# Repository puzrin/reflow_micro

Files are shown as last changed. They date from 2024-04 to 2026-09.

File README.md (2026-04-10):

Reflow Micro Table
==================

> Compact Bluetooth-controlled reflow table with an 80x70 mm working area.
> Built for hobby projects when you do not want a bulky professional machine
> taking over your desk.

- [Documentation](doc/README.md)
- [EasyEDA project page](https://oshwlab.com/puzrin/reflow-table-pd) -
  Schematic & PCB. Order almost everything in a couple of clicks.
- [Hackaday.io](https://hackaday.io/project/204503-reflow-micro-table) page.

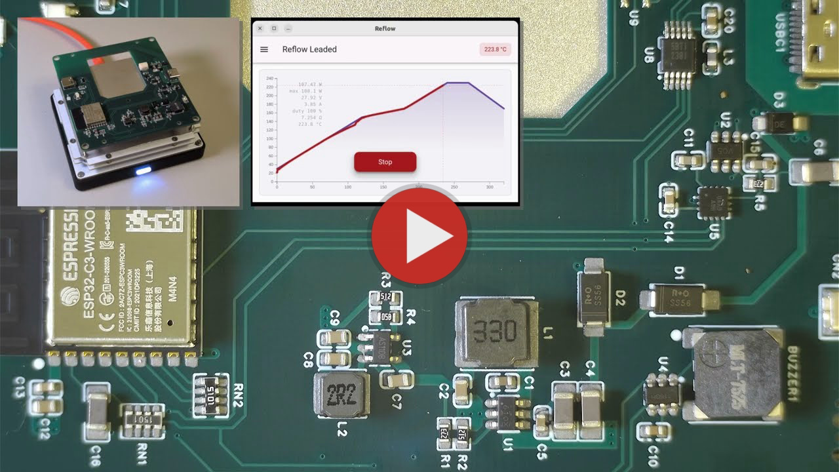
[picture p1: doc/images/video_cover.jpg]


## Description

This table is meant for hobbyists who assemble PCBs from time to time. It may
not be as feature-packed as professional gear, but it's compact and covers most
hobby needs.

Key points:

- Very compact and easy to store when not in use.
- Powered from a 100-140 W USB PD charger.
- Controlled from a web browser (desktop and mobile).
- 80x70 mm working area.
- Components cost about 85$ with the simple MCPCB heater, 105$ with the MCH
  heater.
- Simple heating profile management.
- Up to 180°C with the simple MCPCB-based head.
- Up to 250°C with the MCH-based head.

Use cases:

- Reflow soldering with Sn42Bi58 (138°C) paste using the MCPCB-based head.
- Pre-heating (130-150°C) for hot air work.
- Reflow soldering with Sn63Pb37 (183°C) paste using the MCH-based head.
- Other tinkering, like drying parts or baking paint.

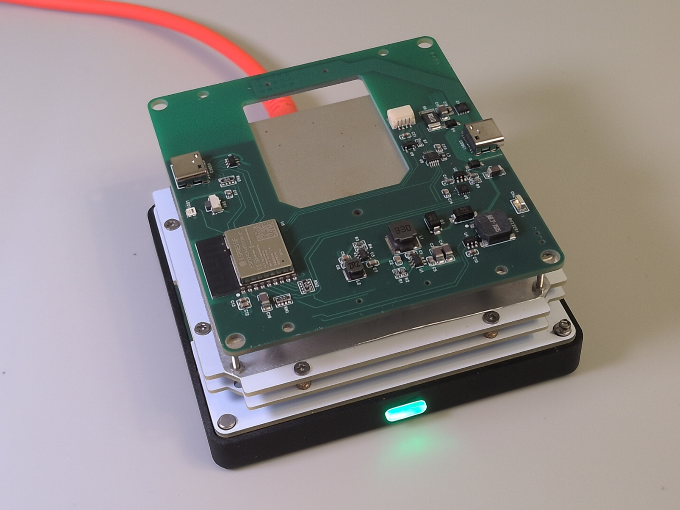
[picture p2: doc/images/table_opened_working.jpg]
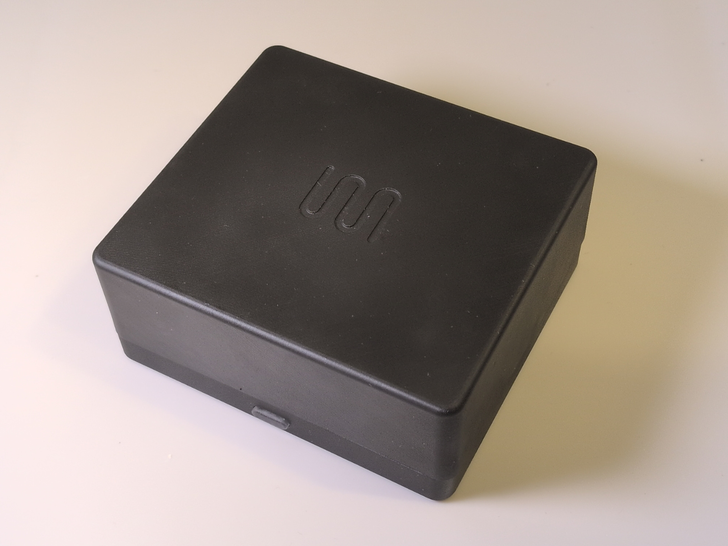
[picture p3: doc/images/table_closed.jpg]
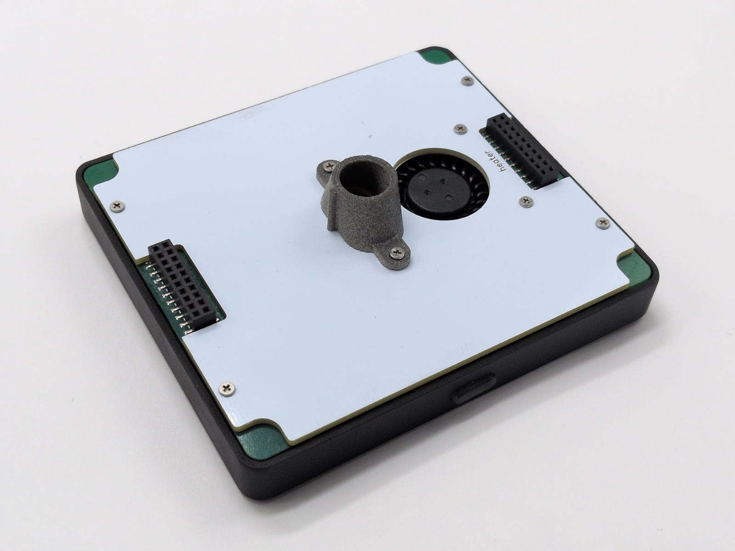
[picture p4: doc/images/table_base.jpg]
  <br />
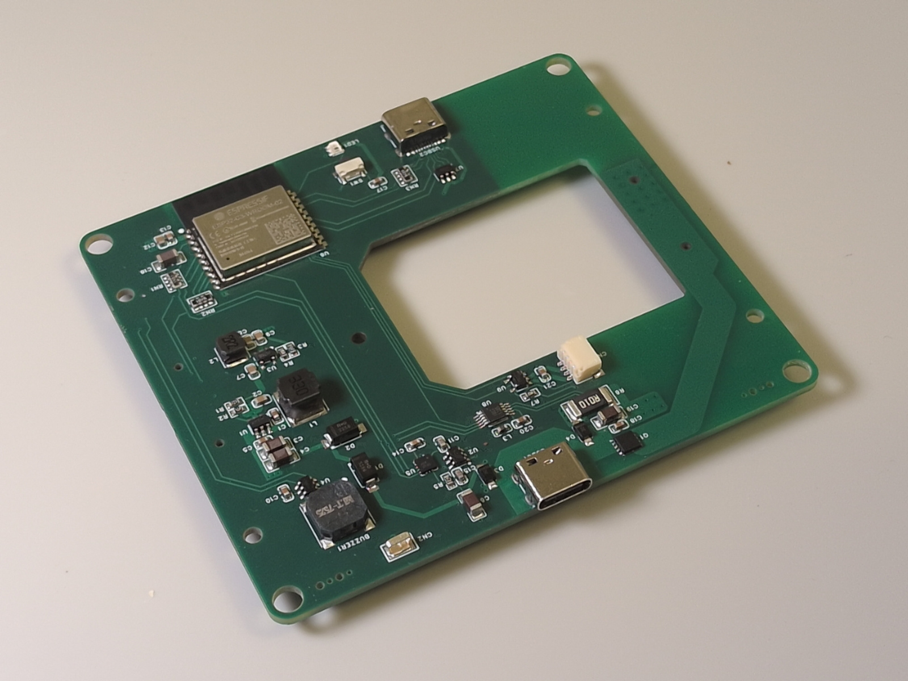
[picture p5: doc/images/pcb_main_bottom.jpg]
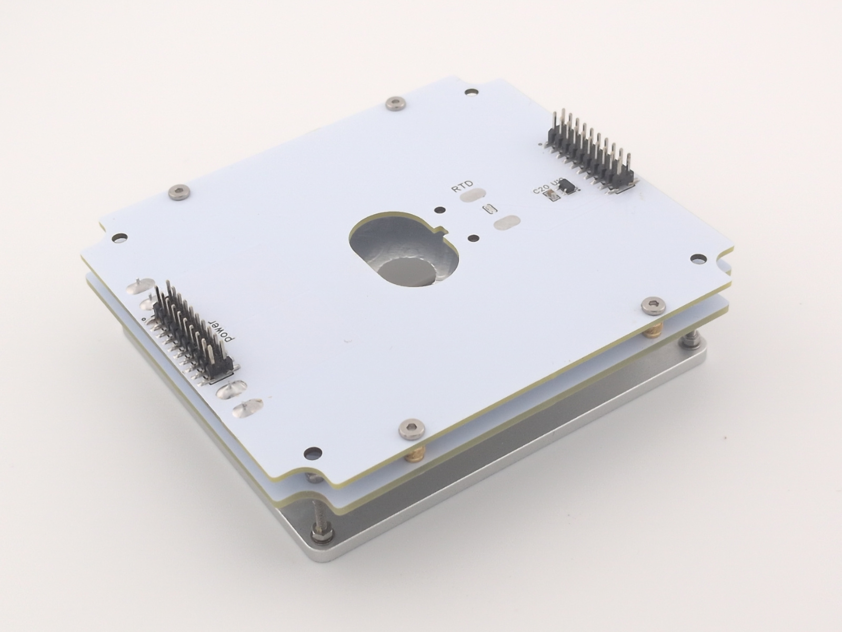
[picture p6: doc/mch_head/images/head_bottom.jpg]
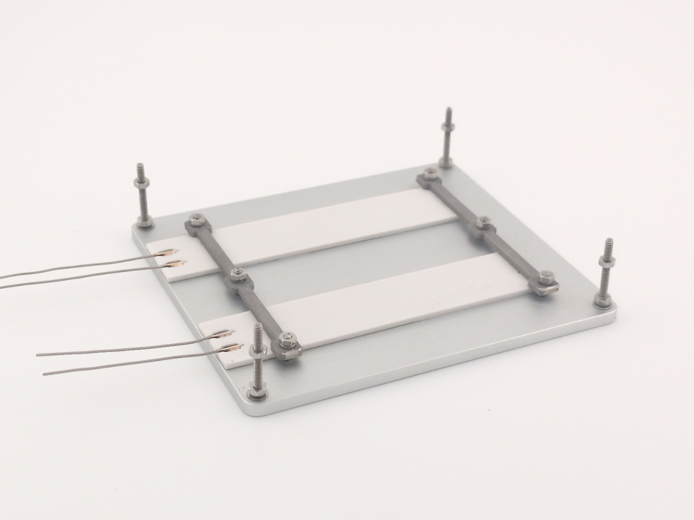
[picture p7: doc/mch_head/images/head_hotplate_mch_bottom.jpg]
  

> [!NOTE]
>
> This project was built to set a higher standard in this class. It also shows
> beginners that the technologies behind modern electronics are accessible
> today. Even at home, it is now possible to build complex devices that match
> factory-made products, and in some cases go beyond them.

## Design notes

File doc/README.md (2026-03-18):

Reflow Table Documentation
==========================

IMPORTANT: Read all documentation carefully before ordering anything!
By default, the BOM includes components only for the simple, low-cost MCPCB
heater intended for LTS pastes. The advanced MCH head and its BOM are
described in a separate document.

## Read first

- [bom.md](./bom.md) - bill of materials.
- [build.md](./build.md) - build guide.
- [heating_heads.md](./heating_heads.md) - overview of the available heaters
  and their limits.
- [soldering_paste.md](./soldering_paste.md) - quick notes for beginners on
  soldering paste.
- [calibration.md](./calibration.md) - how to tune the device after assembly.
- [user manual](./user_manual.md) - how to use the device.

## Advanced

- [mch_head](./mch_head/) - details on the advanced heater, up to 250°C.
- [modeling](./modeling/) - Python notebooks for simulating the heating process
  in different conditions.

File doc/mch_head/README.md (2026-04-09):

MCH-based heating head <!-- omit in toc -->
======================

- [BOM](#bom)
- [MCH heater resistance matching](#mch-heater-resistance-matching)
- [Cut SS clamps](#cut-ss-clamps)
- [Mount hotplate top parts](#mount-hotplate-top-parts)
- [Mount reflector](#mount-reflector)
- [Mount base](#mount-base)

## BOM

This BOM extends the default one; be sure to order it as well.

&nbsp; | Name | Comment
-------|------|--------
1 | Hotplate and clamps | See details below.
2 | M1.6 countersunk SS screws 8 mm (×6) | [EDLW-S1-M1.6-L8](https://jlcmc.com/product/s/E02/EDLW/gb-t-819-phillips-countersunk-head-screw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). MCH mount.
3 | [MCH 70*14 2R (×2)](https://www.aliexpress.com/item/32966428374.html) | Two heaters are required; buy 5-10 so you can match their resistance.
4 | [Thermally conductive paste](https://www.aliexpress.com/item/1005009116482403.html) | [Alternate](https://www.aliexpress.com/item/1005011659620916.html) (more expensive, but up to 350°C).

> [!NOTE]
>
> Thermal paste should be durable at 250°C (leaded profile rises to 230°C).
> Pastes from 3D printer hotends are good candidates. Look for "Creality Thermal
> Grease" (250°C) and "Creality High-Temperature Thermal Grease" (350°C) first.
> Avoid computer pastes; their max temperature is not guaranteed even if
> declared.

**Hotplate (JLCCNC)**:

- File `hotplate_80x70x2.8.step`
  - Material: Aluminum 6061.
  - Surface Finish: "Anodizing" (Natural color, matte).
  - Comment: "Face mill both top and bottom flat surfaces. No raw stock surface acceptable."

**MCH mounting (JLC3DP)**

- File `ss_mch_mount.stl`
  - `SLM(Metal)` process, 316L steel. Don't try `BJ(Metal)`; it will be rejected.
  - Comment: "All defects are acceptable in advance." The design is on the edge
    of the printing requirements, so this comment helps avoid order declines.

**Thermal paste stencil (JLCPCB)**

This is optional. It makes applying the thermally conductive paste easier.

https://oshwlab.com/puzrin/reflow-table-pd

- `thermal_paste_stencil`
  - Top side only.
  - Custom size 100x46 mm.
  - Thickness 0.1 mm.
  - Select "Confirm production file".
  - Comment "**Make stencil according to paste mask file**".

**Thermal paste conductor (JLC3DP)**

This stencil conductor is also optional.

- File `thermal_paste_conductor.stl`
  - SLA, LEDO 6060.

**Optional**

Treat this as a checklist; pick what you are missing from your bench.

&nbsp; | Name | Comment
-------|------|--------
1 | [Dental diamond disks](https://www.aliexpress.com/item/4001138228461.html) | For cutting the stainless clamps. Grab a mandrel too.
2 | Phosphoric Acid | To tin MCH wires if you don't have another active flux. [Dental Etchant Gel](https://www.aliexpress.com/i/1005006254467176.html) works pretty well. Soldering tip cleaner should be okay too, but it is less convenient than gel.

## MCH heater resistance matching

The build uses two MCH heaters, so their resistance needs to match closely for
balanced heating. Buy a few extras so you can pair them.

> [!NOTE]
>
> Aim for roughly 2% tolerance.

After the main board is assembled and flashed, use a temporary head base board
with a wire connector:

- Connect the device and open `Measure resistance` in `Settings`.
- Swap MCH heaters and record the resistance of each one.
- Sort by resistance and select the best-matched pairs.

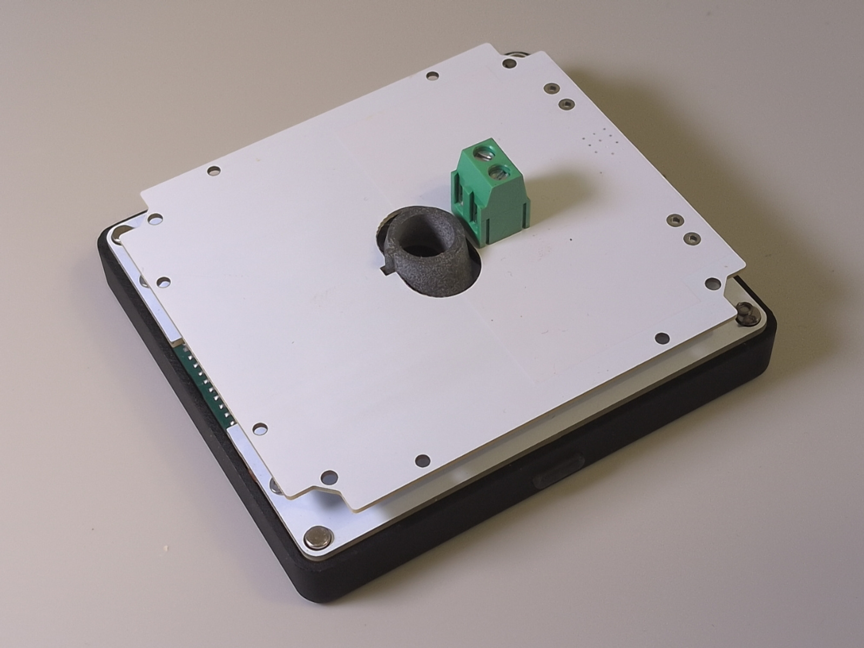
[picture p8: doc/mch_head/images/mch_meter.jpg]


> [!TIP]
>
> - Make sure the wire lengths are similar for all MCHs when measuring.
> - Buying ten heaters typically yields 3-4 usable pairs. Five heaters
>   typically yield 1-2 pairs.

TBD: image

## Cut SS clamps

Cut the stainless steel clamps free from the panel. A Dremel with thin dental
diamond disks works very well and keeps the cuts precise.

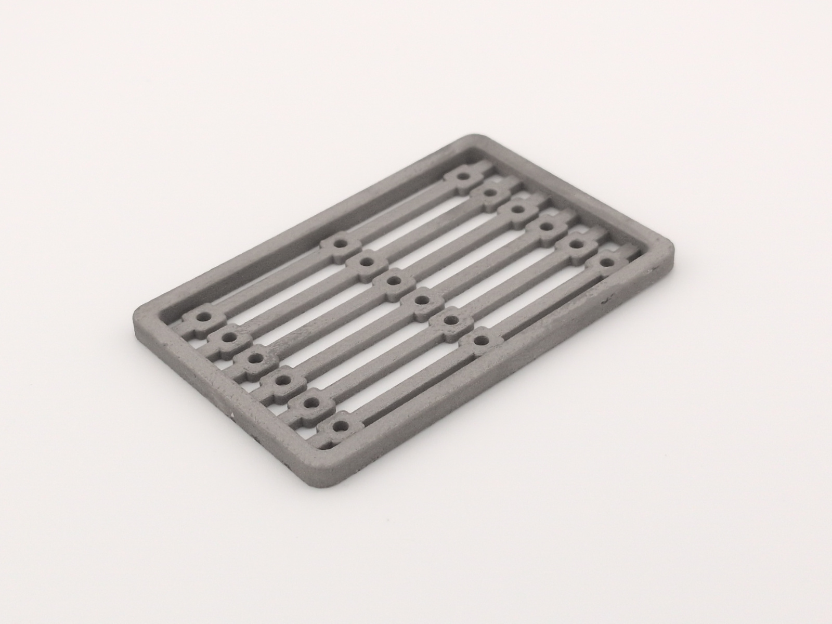
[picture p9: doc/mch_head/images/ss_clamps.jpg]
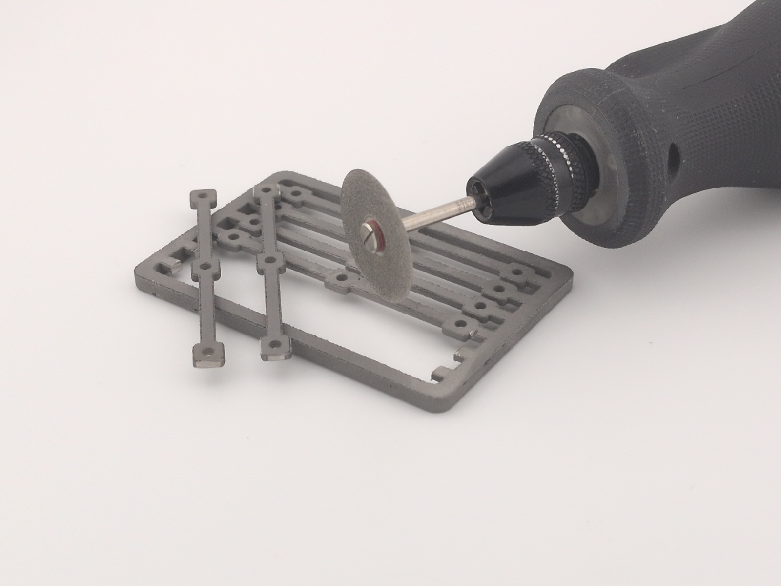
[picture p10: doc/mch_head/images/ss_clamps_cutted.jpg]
 

## Mount hotplate top parts

- Apply a very thin layer of thermal paste to the heaters.
- Place the heaters on the plate and slide them about +/-0.5 mm to spread the
  paste.
- Tighten the screws with spring washers using only a light touch.

Use 8 mm screws for the heaters and 18 mm screws for the corners.



> [!CAUTION]
>
> Do not overtighten the screws; the MCH can crack after heating!

Once everything is mounted, cut the MCH wires to the required length and tin
the ends.

- Usually, a hot iron tip with plenty of solder and ordinary flux is enough.
  Try tinning the cut wires first to make sure it works.
- If you have problems, use active flux. Alternatives include "dental etchant
  gel" or "iron tip refresher".
- Remember to clean the wires after using active flux.

## Mount reflector

Use the conductor as a template to cut the foil reflector, then punch the holes
using a screw.

- Place the foil on a flat surface with the template on top.
- Cut the foil along the template outline and the central hole with a knife.
- Secure the foil to the template with tape to prevent shifting.
- Punch the mounting holes by pressing through with a screw.
- Clean up the foil burrs around the holes by scraping with a tilted screw.

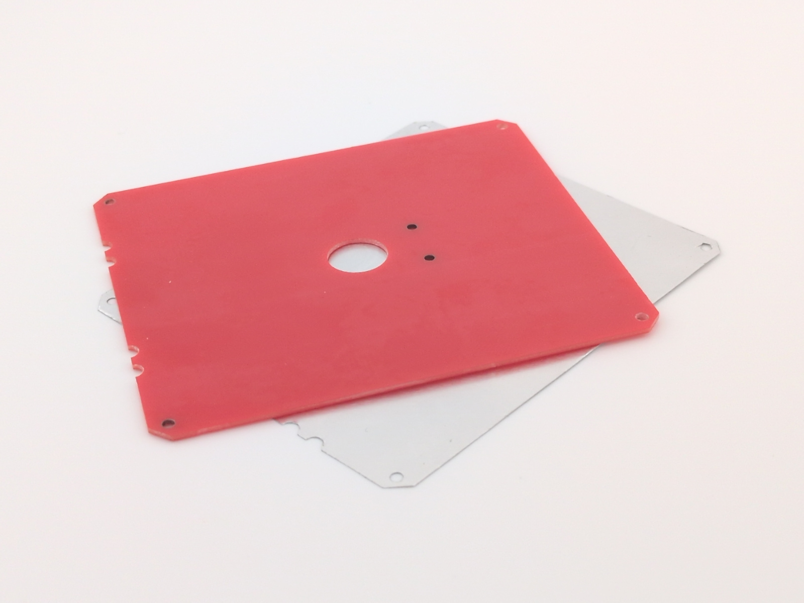
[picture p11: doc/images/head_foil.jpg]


Install the foil and frame on the hotplate.

- Use spacers to set a 12 mm gap between the heater top and the reflector.
- For each corner, insert the spacer, snug the top nut first, then tighten
  the bottom nut; spring lock washers go underneath.

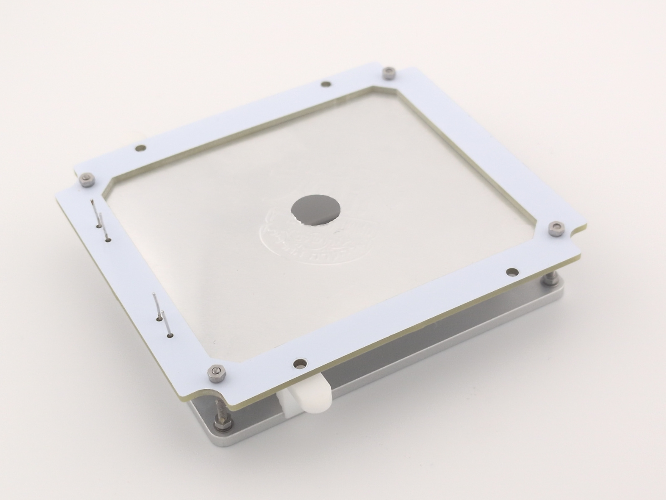
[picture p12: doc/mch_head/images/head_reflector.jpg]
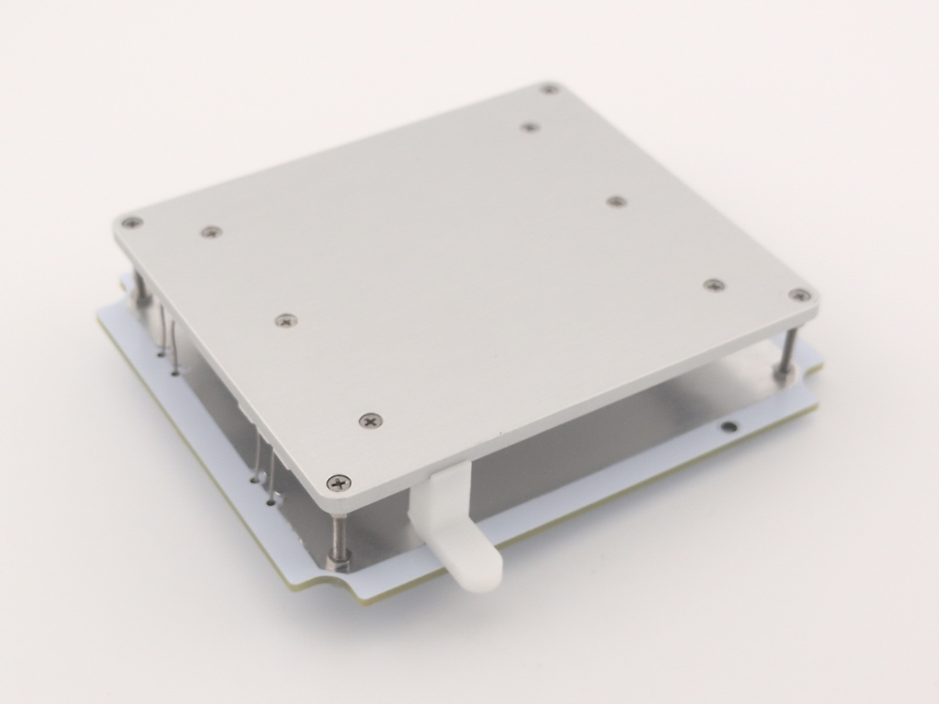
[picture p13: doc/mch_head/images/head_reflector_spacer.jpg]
 

## Mount base

Assemble and mount the base board the same way as described in the
[main build guide](../build.md).

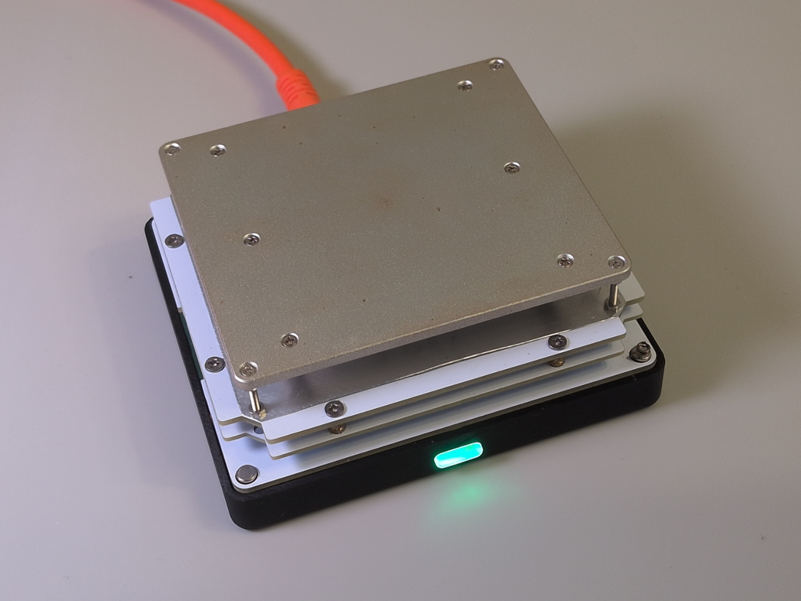
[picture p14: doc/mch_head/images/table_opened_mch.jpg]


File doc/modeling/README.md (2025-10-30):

Use [nbviewer](https://nbviewer.org/) to browse the notebooks online.

- [modeling.ipynb](https://nbviewer.org/github/puzrin/reflow_micro/blob/master/doc/modeling/modeling.ipynb) - Heating graphs for different heaters so you can check performance.
- [calibration_views.ipynb](https://nbviewer.org/github/puzrin/reflow_micro/blob/master/doc/modeling/calibration_views.ipynb) - R, TCH, and HTC graphs based on calibration data for quick visual checks.
- [adrc.ipynb](https://nbviewer.org/github/puzrin/reflow_micro/blob/master/doc/modeling/adrc.ipynb) - ADRC controller parameter modeling.

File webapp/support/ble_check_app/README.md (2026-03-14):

Test app for experimenting with BLE transport and measuring performance.

Before you start:

- In the firmware build, set the `BLE_TEST` environment variable to enable the test RPC methods.

Run:

```sh
npm i
npm start
```

On the first connection, press the device button five times quickly to pair over BLE.

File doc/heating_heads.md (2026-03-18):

Heating Heads
=============

The reflow table supports two heater types you can build at home without
industrial tools or a dedicated workshop.

Keep in mind that this table uses a bottom-heating approach, which is a
compromise between compactness and feature richness. It shines in a home hobby
setup, but for professional use you may still want a larger, more advanced
reflow oven.

When a reflow profile runs, there's no cover cap and all heat comes from the
bottom. The plate and the top of the PCB can differ by as much as 20°C. Using
low-temperature (138°C) paste gives you plenty of margin, forgives minor
mistakes, and keeps the heater requirements modest.

## Aluminum PCB-based heater

**Pros:**

- Very affordable.
- Easy to build.
- A 100 W charger is fine for an 80x70 mm plate.

**Cons:**

- Max temperature is only 180°C.
- Runs above the MCPCB's MOT (130°C) and will slowly degrade, but it's fine for
  hobby use that isn't 24/7.

Conclusion:

- Great for hobby builds that use LTS soldering.
- Handy as a bottom pre-heater for hot air work with leaded or RoHS pastes.
- Overall, it's the recommended starting point.

## MCH-based heater

**Pros:**

- Safe up to 250°C.
- Suitable for both LTS and SnPb pastes.

**Cons:**

- A bit more expensive and involved, with more components to buy.
- Needs a 140 W supply.
- Performance above 200°C is not ideal: roughly 1°C per second.

Conclusion:

- LTS and SnPb pastes will be ok, but do not expect good results with RoHS
  paste.

> [!NOTE]
>
> With upcoming PD 3.2 chargers (end of 2026) pushing more power into these
> heaters will be easier.

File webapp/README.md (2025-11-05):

# Reflow Micro web UI

Vue 3 + TypeScript single-page app that talks to the Reflow Micro table over Web Bluetooth.

## Requirements

- Node.js 20+
- npm 10+

## Install

```sh
npm install
```

## Common scripts

- `npm run dev` — start the Vite dev server on http://localhost:5173
- `npm run build` — run `vue-tsc` and produce the production bundle in `dist/`
- `npm run preview` — preview the latest production build
- `npm run test` — lint, type-check, and run the Vitest suite
- `npm run lint:fix` — auto-fix lint issues where possible
- `npm run format` — format the sources with Prettier

## Protobuf sources

Message formats live in `src/proto/types.proto`. To regenerate all artifacts (TS types, firmware stubs, and default payloads), run:

```sh
npm run gen:proto
```

This command shells out to `protoc`, `nanopb_generator`, and `ts-proto`. They are installed via dev dependencies; ensure you have Python available for `nanopb_generator`.

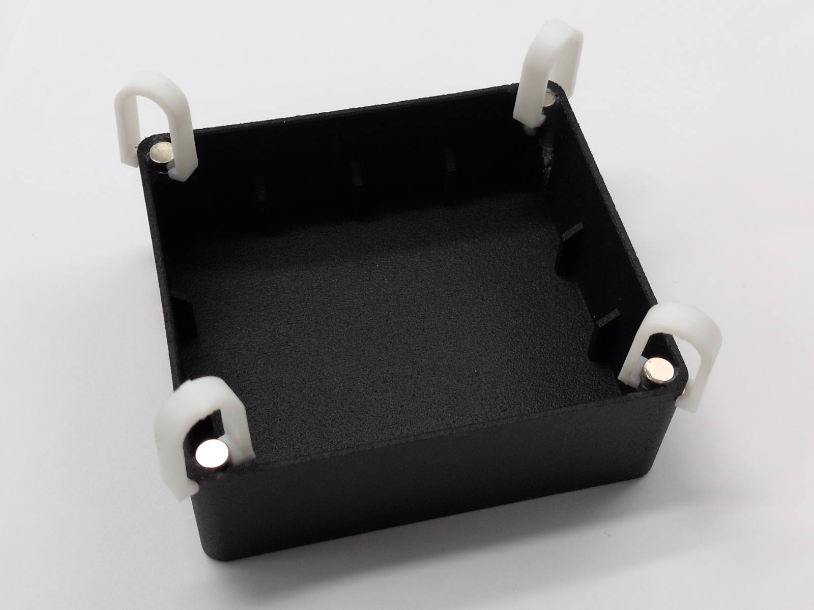
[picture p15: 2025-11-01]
doc/images/case_glued_cap.jpg

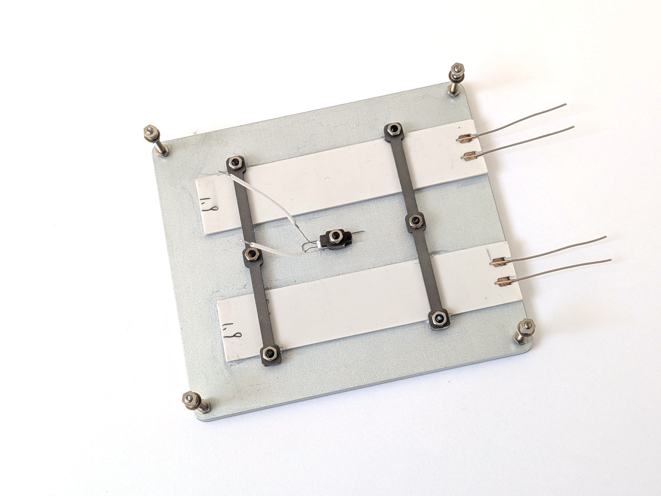
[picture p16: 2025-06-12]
doc/mch_head/images/head_top_back.jpg

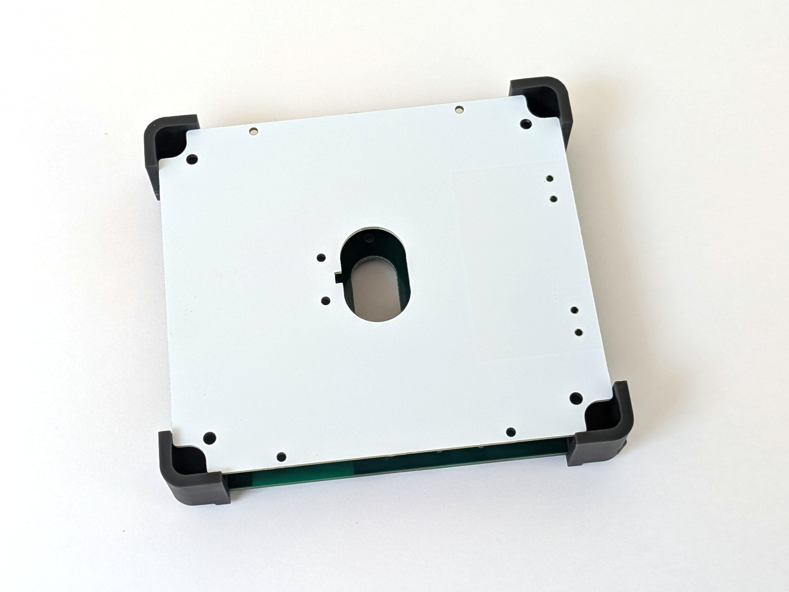
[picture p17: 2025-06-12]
doc/mch_head/images/pcb_with_head_base.jpg

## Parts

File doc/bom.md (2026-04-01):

Bill of Materials
=================

> [!NOTE]
>
> This BOM does not include MCH heater components. See the
[separate document](./mch_head/README.md) for details. It adds about $30 to
the cost.

### General

&nbsp; | Name | Comment
-------|------|--------
1 | [PCB & Components](https://oshwlab.com/puzrin/reflow-table-pd) | Open the EasyEDA project and order both in a couple of clicks. Order the PCB first and the components second so the shipments can be combined.
2 | Location pins 1.0 or 0.6 mm | For SMT stencil positioning. [FDWQ-M1-D1-L10](https://jlcmc.com/product/s/F02/FDWQ/hexagonal-flange-face-self-tapping-drill-tail-screw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) / [AliExpress](https://www.aliexpress.com/item/1005007439330472.html). Any 1.0/0.6 mm wire will also work.
3 | M1.6 countersunk SS screws 16 mm (×4) | [EDLW-S1-M1.6-L16](https://jlcmc.com/product/s/E02/EDLW/gb-t-819-phillips-countersunk-head-screw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). Mount the heater plate to the reflector. Make sure they are stainless steel.
4 | M1.6 SS flat washers (×4) | [EPDA-S1W-B-1.6](https://jlcmc.com/product/s/E06/EPDA/flat-washer-level-a?k=EPDA-S1W-B-1.6&productModelNumber=EPDA-S1W-B-1.6). Hotplate mount.
5 | M1.6 SS spring lock washers (×8) | [EPDC-S1W-1.6](https://jlcmc.com/product/s/E06/EPDC/spring-washer-standard-spring-washers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). Hardware for the head mount.
6 | M1.6 SS nuts (×12) | [EMLA-S1W-BL1-M1.6](https://jlcmc.com/product/s/E04/EMLA/hex-nut-standard-thin-thickened-coarse-fine-thread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). Hardware for the head mount.
7 | M2 screws 3 mm (×14) | [EDDM-M2-L3](https://jlcmc.com/product/s/E02/EDDM/phillips-ultra-thin-head-screw?k=EDDM-M2-L3&productModelNumber=EDDM-M2-L3). Mount the reflector to the head base.
8 | M2 screws 10 mm (×10) | [EDLU-S1-M-M2-L10](https://jlcmc.com/product/s/E02/EDLU/gb-t-818-823-phillips-pan-head-screw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). Mount the fan and PCB.
9 | M2 nuts (×10) | [EMLA-S1W-BL1-M2](https://jlcmc.com/product/s/E04/EMLA/hex-nut-standard-thin-thickened-coarse-fine-thread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). Mount the fan and PCB.
10 | M3 countersunk hex screws 10 mm (×4) | [EDLJ-C16-M3-L10](https://jlcmc.com/product/s/E02/EDLJ/din-7991-gb-t-70.3-hex-socket-countersunk-head-screw). Black finish. Part of the cap's magnetic latch. The material should be magnetic; any non-stainless steel should work.
11 | [M2 4 mm insert nuts (×7)](https://www.aliexpress.com/item/1005008644449489.html) | Hardware for the head mount.
12 | [Magnets D6 L3 (×8)](https://www.aliexpress.com/item/1005010676875849.html) | Cap latch. N52 preferred, look for "magnets for 3d printers".
13 | [Magnets D4 L4 (×4)](https://www.aliexpress.com/item/1005010676875849.html) | Cap latch (two D4 L2 magnets are also fine). N52 preferred, look for "magnets for 3d printers".
14 | [Raspberry Pi 5 fan](https://www.aliexpress.com/item/1005006547048892.html) | Side-blowing fan for plate cooling.
15 | [AWG 26 wire](https://www.aliexpress.com/item/1005010779278423.html) | For the MCPCB head power wires only. Any 0.4 mm (0.126 mm²) tinned copper wire will work. The small cross-section helps reduce heat transfer.
16 | [Vinyl Electrical Tape 0.15 mm, black](https://www.aliexpress.com/item/1005010360658475.html) | For SLA prints only. Use it when installing M3 screws into the cap.

> [!NOTE]
>
> - Be sure to order components from both `main` and `head_base_XX` boards.
> - If male connectors with boss pins (Liansheng FH-00147) are not available,
>   use any SMD 2 mm 2x10P connectors with a height of 4.6 mm or less (body + pins).

### Optional

Treat this as a checklist; pick what you are missing from your bench.

&nbsp; | Name | Comment
-------|------|--------
1 | 140 W USB PD charger | Support for PPS 5-21 V / 5 A profiles is mandatory. A 28 V profile is required for the MCH heater (a 100 W charger is fine for the MCPCB heater). Single-port chargers are cheapest (25-30 USD). [Link 1](https://www.aliexpress.com/item/1005009049417279.html), [link 2](https://www.aliexpress.com/item/1005008926893357.html).
2 | [K-probe thermometer](https://www.aliexpress.com/item/1005008715777280.html) | For temperature calibration. The TM-902C from AliExpress is inexpensive and accurate enough.
3 | [Soldering air gun](https://www.aliexpress.com/item/1005006099512955.html) | For PCB assembly.
4 | Low-temp soldering paste | Sn42Bi58, 138°C, for PCB assembly. Standard leaded paste works too, but low-temp paste is more convenient.
5 | 217°C soldering paste | Use it on the PCB heater power lines.
6 | [Heat-set insert tip](https://www.aliexpress.com/item/1005009572892377.html) | For a nylon (PA-12) case only. Select the one that fits your iron.
7 | [Zero-flute countersink](https://www.aliexpress.com/item/1005004217081267.html) | Select the 1 mm size. For the MCPCB head only, countersink the MCPCB-based hotplate so the screw heads sit flush.

## JLCPCB / LCSC order notes

https://oshwlab.com/puzrin/reflow-table-pd

1. `main`: 1.6 mm, green (other colors for 4-layer PCBs are pricey).
   - Stencil is strongly recommended; it adds roughly $3 to the order and saves
     a ton of effort:
     - Bottom side only.
     - Select "Custom size" and set 90 x 80 mm (so the stencil stays compact and
       lightweight, keeping delivery costs down).
     - Select "Confirm production file" to ensure the positioning holes are generated correctly.
     - Add this comment: "**Make marked blocks of holes (near top corners) on the stencil
       too. See doc layer for details.**". Otherwise, the positional holes might be missed.
2. `cap`: 1.6 mm, white.
3. `head_base_2R`: 1.2 mm, white.
4. `head_reflector`: 1.6 mm, white.
5. `mcpcb_heater`: aluminum, 1.6 mm, 1 oz.
   - Simple and cheap, but only up to 180°C.
   - For 250°C, see the [MCH heater](./mch_head/README.md) details (with the
     extra BOM).
6. `foil_conductor`: 1.0 mm, red.

JLC3DP prints:

1. `tray`, `cap_xxx`: SLA "JLC black resin" or MJF "PA12-HP nylon, black".
   - SLA: okay, budget price.
   - Nylon: about twice as expensive as SLA, but better-looking.
   - (!) With nylon, use `cap_mjf_pa12` (smaller holes for self-tapping screws). For
     SLA, use `cap_sla`.
2. `air_duct_pi5_top`, `air_duct_pi5_bottom`: MJF "PA12-HP nylon", unpainted (natural color).
3. `button`: SLA "8001 resin", translucent.
4. `tool_spacer`: SLA "9600 resin".
5. `pcb_aligner`: SLA "9600 resin".
6. `drill_conductor`: SLA "9600 resin" (for MCPCB heater only).

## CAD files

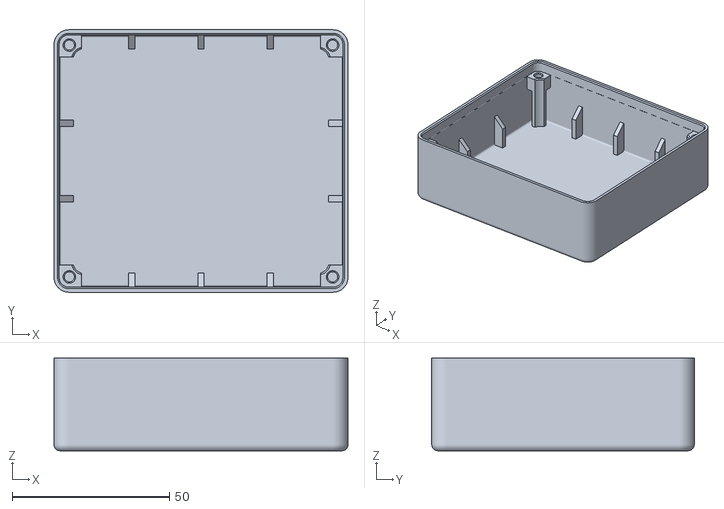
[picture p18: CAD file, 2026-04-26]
3dparts/cap_sla.stl
93.5 x 83.5 x 29.5

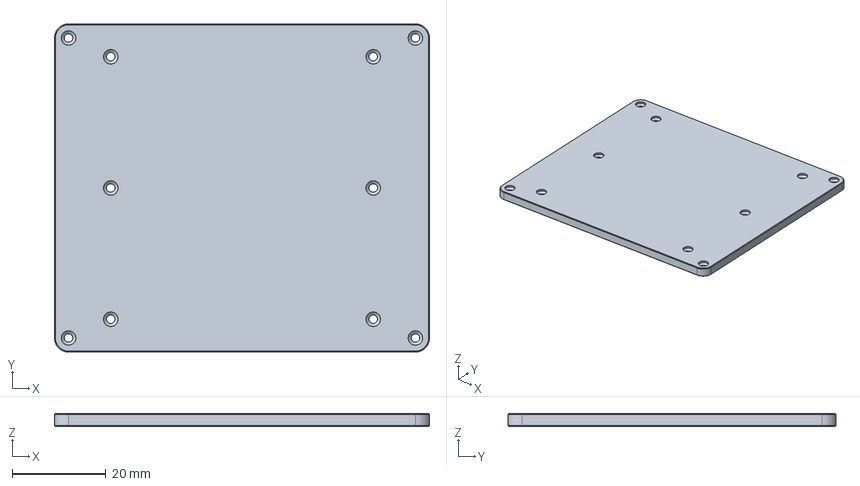
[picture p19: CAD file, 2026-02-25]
3dparts/mch_head/src/hotplate_tcr_2mch_80x70x2.8.FCStd
80.0 x 70.0 x 2.80 mm

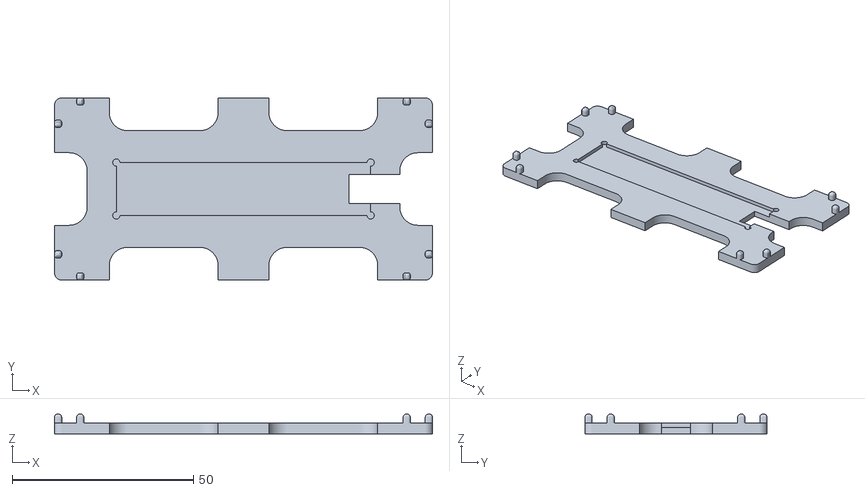
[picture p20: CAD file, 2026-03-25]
3dparts/mch_head/thermal_paste_conductor.stl
104.2 x 50.2 x 5.49

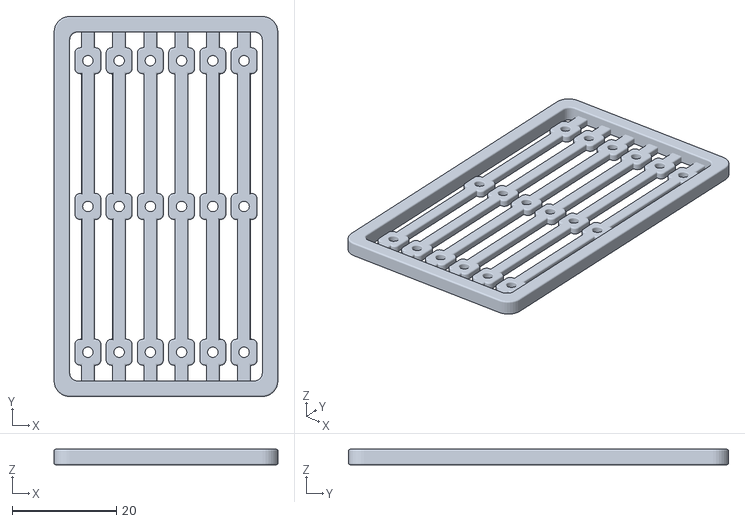
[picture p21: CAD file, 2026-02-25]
3dparts/mch_head/ss_mount_2mch.stl
43.0 x 73.0 x 3.00

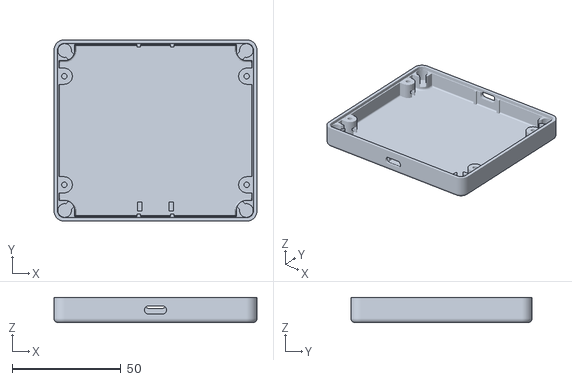
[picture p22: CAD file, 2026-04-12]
3dparts/tray.stl
93.5 x 83.5 x 11.7

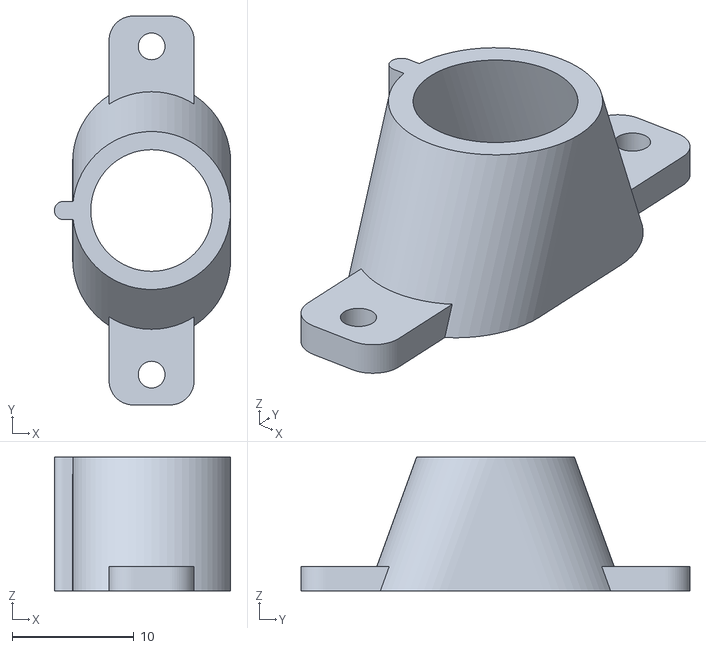
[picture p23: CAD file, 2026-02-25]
3dparts/air_duct_pi5_top.stl
14.5 x 32.0 x 11.0

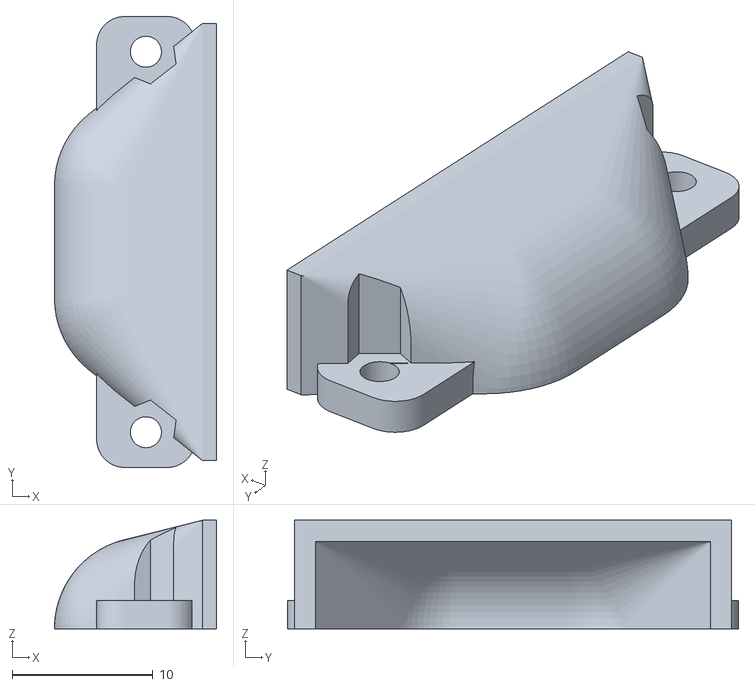
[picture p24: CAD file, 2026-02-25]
3dparts/air_duct_pi5_bottom.stl
11.5 x 32.0 x 7.70

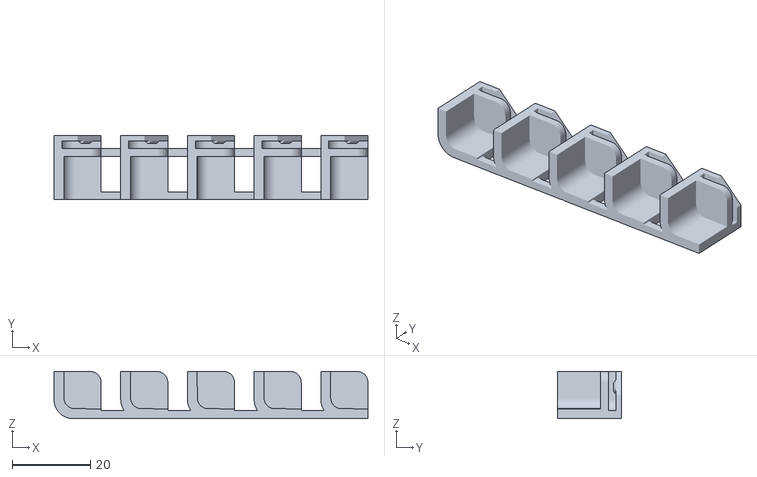
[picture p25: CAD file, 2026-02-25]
3dparts/pcb_aligner.stl
80.0 x 16.4 x 12.0

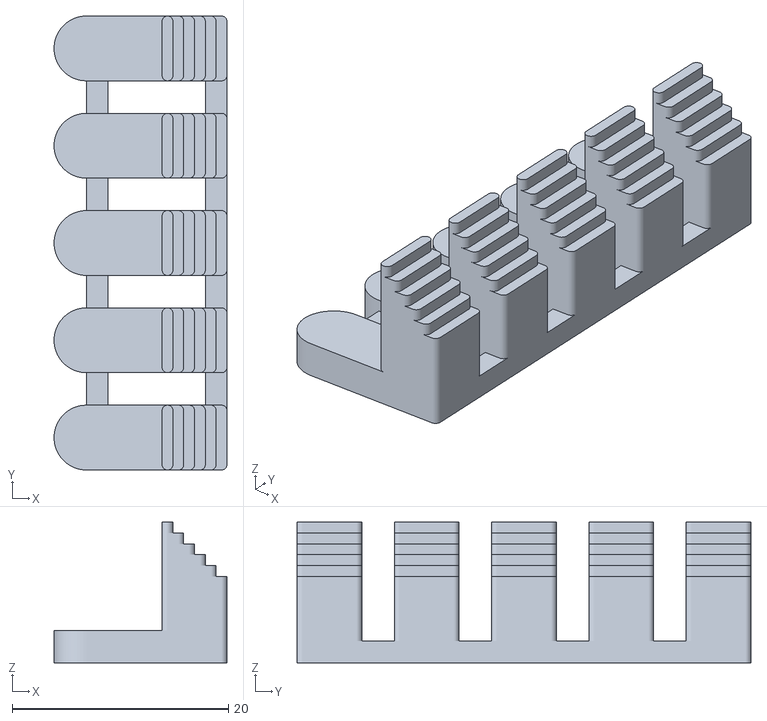
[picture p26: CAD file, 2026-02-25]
3dparts/tool_spacer.stl
16.0 x 42.0 x 13.0

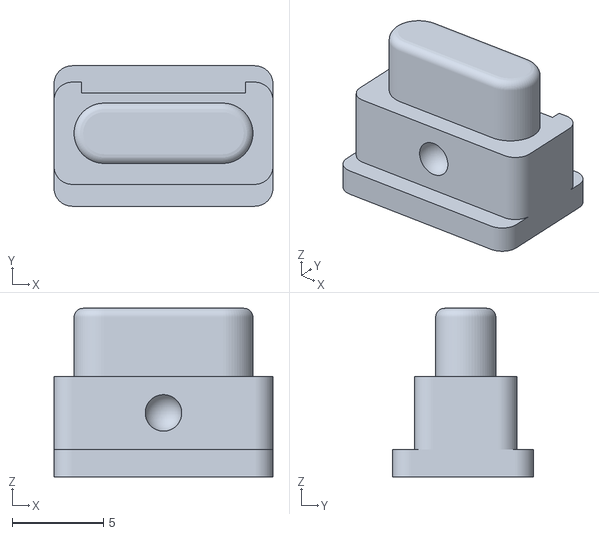
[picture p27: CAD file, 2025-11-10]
3dparts/button.stl
12.0 x 7.70 x 9.24

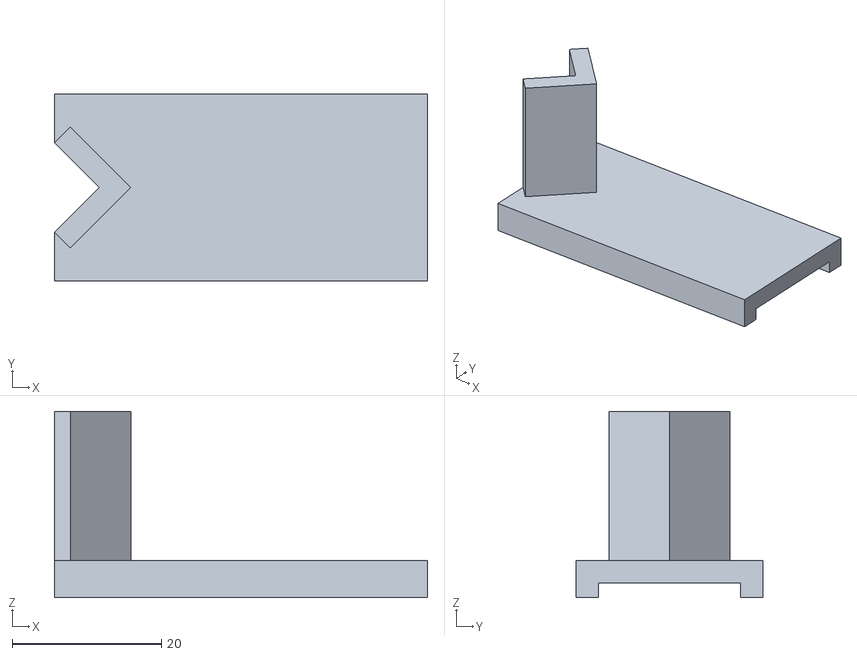
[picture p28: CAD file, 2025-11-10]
3dparts/drill_conductor.stl
50.0 x 25.0 x 25.0

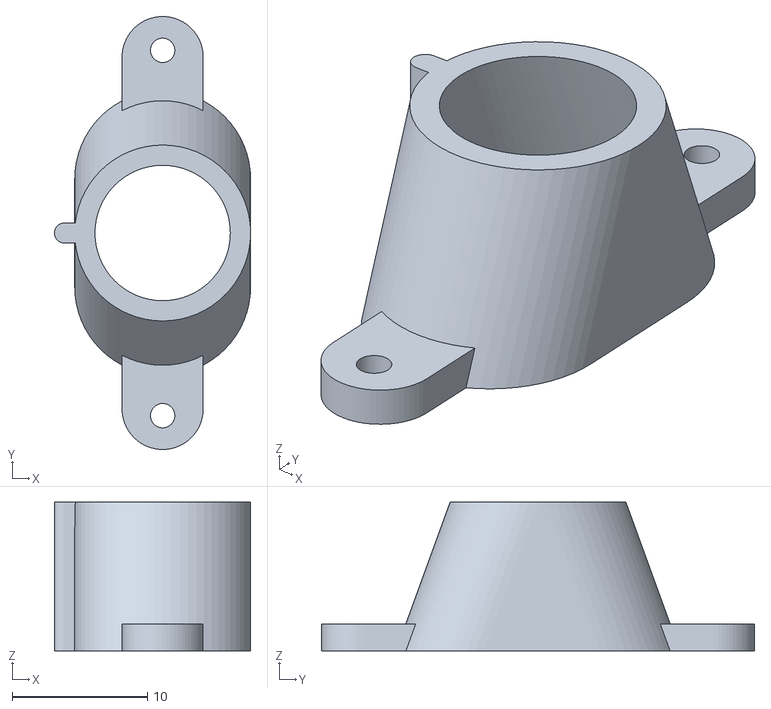
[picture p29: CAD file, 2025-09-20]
3dparts/air_duct_pi5_top_11.stl
14.5 x 32.0 x 11.0

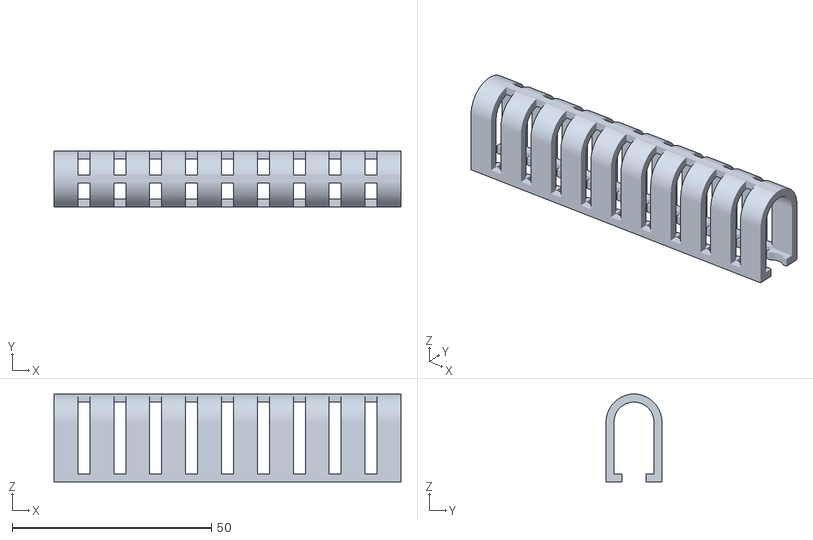
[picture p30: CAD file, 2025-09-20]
3dparts/magnet_clamp.stl
87.0 x 14.0 x 22.0

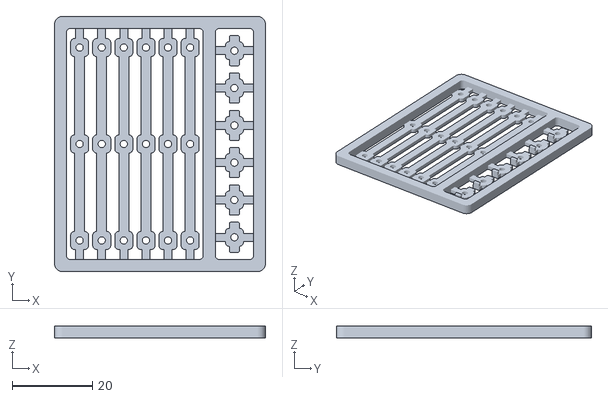
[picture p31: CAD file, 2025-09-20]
3dparts/ss_mch_mount.stl
52.5 x 63.5 x 3.00

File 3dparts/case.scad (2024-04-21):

include <utils.scad>;

$fn = $preview ? 16 : 64;

// Inserts size for PCB mount (M1.6)
insert_d = 2.5 + 0.1;
insert_h = 4 + 0.5;
insert_pcb_x_offset = 3;

// !!! Measure magnets height before case order.
// 2 magnets with "3mm" height from aliexpress can be only 5.3-5.4mm total
MAGNET_H = 6;
magnet_d = 6;
magnet_h = MAGNET_H;
magnet_margin_h = 0.1;

wall = 1.5;

pcb_wx = 90;
pcb_wy = 80;
pcb_r= 3;
pcb_support_w = 0.5;
pcb_side_margin = 0.1;
pcb_top_margin = 0.1; // extra space for better cap close
// 1.6 PCB + margin
pcb_h  = 1.6 + pcb_top_margin;

case_wx = pcb_wx + 2*wall;
case_wy = pcb_wy + 2*wall;

case_locker = 1; // ring size to position cap to tray

case_r_vert = pcb_r + wall;
case_r_bottom = 1;
case_r_top = 1;

tray_inner_h = 6.7;
tray_h  = tray_inner_h + wall + pcb_h;

// plate (4) + space (8) + reflector (1.2/1.6) + space (4) + shield (1.2) + extra (1)
cap_inner_h = 4 + 8 + 1.6 + 4 + 1.2 + 1;

cap_h = cap_inner_h + wall;

btn_h = 3;
btn_w = 8;
btn_margin = 0.1;

btn_pusher_w = 10;
btn_pusher_base_w = 1.5;
btn_pusher_pcb_depth = 6;
//btn_ring_w = 0.4;

led_h = 1.1; // 0.8...1.1 for different models

module case_left(ofs = 0) { tr_x(ofs - case_wx/2) children(); }
module case_right(ofs = 0) { tr_x(ofs + case_wx/2) children(); }
module case_front(ofs = 0) { tr_y(ofs - case_wy/2) children(); }
module case_back(ofs = 0) { tr_y(ofs + case_wy/2) children(); }

// esp32 - 3.2mm, USB - 3.26mm
assert(tray_inner_h > 3.5, "Not enougth room for PCB components");

module usb_hole() {
    // outer sizes
    usb_w = 8.94;
    usb_h = 3.26;
    usb_r = 1.52;

    tr_z(-usb_h/2)
    rotate_x (-90) {
        tr_z(-e) rcube([usb_w, usb_h, 10], r=usb_r);

        w = usb_w + 0.2;
        h = usb_h + 0.2;
        mirror_z() rcube([w, h, 10], r=usb_r);
        mirror_y() mirror_z() tr_x(-w/2) linear_extrude(10) square(w, 10);
    }
}

module tray_pcb_support() {
    r = insert_d/2 + wall;

    tr_z(wall-e)
    difference() {
        linear_extrude(tray_inner_h)
        rsquare([2*r, 2*r], r=[0, 0, r, r], center = true);

        tr_z(tray_inner_h+e) mirror_z() linear_extrude(insert_h) circle(r=insert_d/2);
    }
}

module magnet_support(h = 20) {
    r = magnet_d/2;
    reserve_w = 1;
    mh = magnet_h + magnet_margin_h;
    assert(mh <= tray_inner_h, "Tray inner too small for desired magnet height")

    tr_xy(-3.5, -3.5)
    difference() {
        union() {
            linear_extrude(h) circle(r = r);
            rotate_extrude(angle=90) square([r+reserve_w, h]);
        }

        tr_z(h - mh + e) linear_extrude(mh) circle(r = r+e);
    }
}

module magnet_support_4x(h=20) {
    shift = wall+pcb_support_w;

    tr_xy(pcb_wx/2, pcb_wy/2) tr_z(wall-e) magnet_support(h+e);

    mirror_x()
    tr_xy(pcb_wx/2, pcb_wy/2) tr_z(wall-e) magnet_support(h+e);

    mirror_y()
    tr_xy(pcb_wx/2, pcb_wy/2) tr_z(wall-e) magnet_support(h+e);

    mirror_x() mirror_y()
    tr_xy(pcb_wx/2, pcb_wy/2) tr_z(wall-e) magnet_support(h+e);
}

module _tray_base() {
    difference() {
        rcube([case_wx, case_wy, tray_h], r = case_r_vert, rbottom = case_r_bottom);

        // Inner
        tr_z(wall)
        rcube(
            [case_wx-2*wall-2*pcb_support_w, case_wy-2*wall-2*pcb_support_w, tray_h-wall+e],
            r = magnet_d/2
        );

        // PCB placement
        tr_z(tray_h-pcb_h)
        rcube(
            [case_wx-2*wall+2*pcb_side_margin, case_wy-2*wall+2*pcb_side_margin, pcb_h+e],
            r = pcb_r+pcb_side_margin
        );

    }
}


module tray() {
    difference() {
        union() {
            _tray_base();

            magnet_support_4x(tray_inner_h);

            tr_x(-pcb_wx/2 + insert_pcb_x_offset) tray_pcb_support();
            mirror_x() tr_x(-pcb_wx/2 + insert_pcb_x_offset) tray_pcb_support();


            // Button guides
            tr_z(wall-e)
            union () {
                tr_x(btn_pusher_w/2 + 0.1)
                tr_y(-pcb_wy/2 + btn_pusher_pcb_depth + 1)
                mirror_y() cube([2, 4, 1.2]);

                mirror([1, 0, 0])
                tr_x(btn_pusher_w/2 + 0.1)
                tr_y(-pcb_wy/2 + btn_pusher_pcb_depth + 1)
                mirror_y() cube([2, 4, 1.2]);
            }
        }

        // Button hole
        case_front(wall+pcb_support_w+e) tr_z(tray_h/2)
        rotate_x(90)
        linear_extrude(wall+pcb_support_w+2e)
        hull() {
            tr_x(btn_w/2-btn_h/2) circle(btn_h/2 + btn_margin);
            tr_x(-btn_w/2+btn_h/2) circle(btn_h/2 + btn_margin);
        }

        // USB connector
        tr_z(tray_h-pcb_h) tr_y(pcb_wy/2+pcb_side_margin) usb_hole();
    }
}


module cap() {
    union() {
        difference() {
            rcube([case_wx, case_wy, cap_h],
                r = case_r_vert, rbottom = case_r_bottom);

            tr_z(wall)
            rcube([case_wx - 2*wall, case_wy - 2*wall, cap_h-wall+e], r = case_r_vert - wall);

            // Inner for pcb alu cover
            wl = wall - pcb_side_margin;
            tr_z(cap_h - 2)
            rcube([case_wx-2*wl, case_wy-2*wl, cap_h], r = case_r_vert-wl);

        }

        magnet_support_4x(cap_inner_h);
    }
}

module button() {
    btn_middle_h = tray_h/2 - wall;
    btn_inner_depth = btn_pusher_pcb_depth - pcb_support_w;
    // Calculate back size to leave 0.2mm to led
    btn_back_h = (tray_inner_h - led_h - btn_middle_h - 0.2)*2;

    // "ring" should be > 0.3mm
    assert(btn_back_h - btn_h > 0.3*2, "Too few space for button");

    // temporary guides
    //tr_z(tray_inner_h) linear_extrude(0.1) square(10, center=true);
    //tr_z(tray_inner_h-led_h) linear_extrude(0.1) square(10, center=true);
    //tr_z(-0.1) linear_extrude(0.1) square(10, center=true);

    //tr_z(btn_middle_h) rotate_x(-90)
    difference () {
        union () {
            // Front part, 1mm out of case
            tr_z(btn_inner_depth - e)
            linear_extrude(wall + pcb_support_w + 1)
            rsquare([btn_w, btn_h], r=1.5);

            // Inner
            linear_extrude(btn_inner_depth)
            rsquare([btn_pusher_w, btn_back_h], r=0.5);

            // Pusher
            tr_xy(-btn_pusher_w/2, btn_middle_h)
            mirror_y()
            linear_extrude(btn_pusher_base_w)
            rsquare([btn_pusher_w, tray_inner_h-0.2], r=0.5, center=false);

            // extra supports to keep button in the middle of tray hole
            tr_x(-btn_pusher_w/2)
            linear_extrude(btn_inner_depth-0.5) square([1, btn_middle_h]);

            mirror_x()
            tr_x(-btn_pusher_w/2)
            linear_extrude(btn_inner_depth-0.5) square([1, btn_middle_h]);
        }

        // Light mirror
        mside = btn_back_h - 1;
        m_w = btn_pusher_w - 2;

        tr_z(btn_pusher_base_w)
        tr_xy(m_w/2, btn_back_h/2+e) rotate_y(-90)
        linear_extrude(m_w)
        polygon([[0, 0], [mside, 0], [0, -mside]]);
    }
}

DRAW_TRAY = 0;
DRAW_CAP = 0;
DRAW_BTN = 0;

if (!DRAW_TRAY && !DRAW_CAP && !DRAW_BTN) {
    tray();
    tr_x(100) cap();
    tr_x(-70) button();
}
else {
    if (DRAW_TRAY) { tray(); }
    if (DRAW_CAP) { tr_x(100) cap(); }
    if (DRAW_BTN) { tr_x(-70) button(); }
}

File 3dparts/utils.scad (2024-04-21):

e = 0.01;
2e = 0.02;

module torus(r1, r2, $fn = $fn) {
    rotate_extrude(convexity=2, $fn=$fn)
    difference() {
        translate([r1 - r2, 0, 0]) circle(r=r2, $fn=$fn);
        translate([-r2, 0, 0]) square(r2*2, true);
    }
}

module _hooled_toruses(x, y, r_xy, r_z) {
    translate([r_xy, r_xy, 0]) torus(r_xy, r_z);
    translate([x-r_xy, r_xy, 0]) torus(r_xy, r_z);
    translate([r_xy, y-r_xy, 0]) torus(r_xy, r_z);
    translate([x-r_xy, y-r_xy, 0]) torus(r_xy, r_z);
    
    translate([r_z, r_xy, 0]) rotate([-90, 0, 0]) cylinder(y-r_xy*2, r=r_z);
    translate([x-r_z, r_xy, 0]) rotate([-90, 0, 0]) cylinder(y-r_xy*2, r=r_z);
    translate([r_xy, r_z, 0]) rotate([0, 90, 0]) cylinder(x-r_xy*2, r=r_z);
    translate([r_xy, y-r_z, 0]) rotate([0, 90, 0]) cylinder(x-r_xy*2, r=r_z);
    
    translate([r_z, r_z, -r_z])
    rcube([x-r_z*2, y-r_z*2, r_z*2], r = r_xy-r_z, center = false);
}

module rsquare(size = [30, 10], r = [1, 1, 1, 1], center = true) {
    _r0 = is_num(r) ? r : r[0];
    _r1 = is_num(r) ? r : r[1];
    _r2 = is_num(r) ? r : r[2];
    _r3 = is_num(r) ? r : r[3];
    r0 = _r0 ? _r0 : e;
    r1 = _r1 ? _r1 : e;
    r2 = _r2 ? _r2 : e;
    r3 = _r3 ? _r3 : e;

    x = size[0]; y = size [1];

    tx = center ? -x/2 : 0;
    ty = center ? -y/2 : 0;

    tr_xy(tx, ty)
    hull () {
        tr_xy(r0, r0) circle(r0);
        tr_xy(r1, y - r1) circle(r1);
        tr_xy(x - r2, y - r2) circle(r2);
        tr_xy(x - r3, r3) circle(r3);
    }
}

module rcube(size = [10, 10, 10], center = true, r = 1, rtop = 0, rbottom = 0) {
    x = size[0]; y = size[1]; h = size[2];

    tx = center ? -x/2 : 0;
    ty = center ? -y/2 : 0;

    translate([tx, ty, 0]) {
        if (rtop == 0 && rbottom == 0) {
            translate([r, r, 0]) cylinder(h, r = r);
            translate([x-r, r, 0]) cylinder(h, r = r);
            translate([r, y-r, 0]) cylinder(h, r = r);
            translate([x-r, y-r, 0]) cylinder(h, r = r);
            translate([0, r, 0]) cube([x, y-r*2, h]);
            translate([r, 0, 0]) cube([x-r*2, y, h]);
        }
        if (rtop > 0 && rbottom == 0) {
            translate([0, 0, h-rtop]) _hooled_toruses(x, y, r, rtop);
            rcube([x, y, h-rtop], r = r, center = false);
        }
        if (rtop == 0 && rbottom > 0) {
            translate([0, 0, rbottom]) _hooled_toruses(x, y, r, rbottom);
            translate([0, 0, rbottom])
            rcube([x, y, h-rbottom], r = r, center = false);
        }
        if (rtop > 0 && rbottom > 0) {
            translate([0, 0, h-rtop]) _hooled_toruses(x, y, r, rtop);
            translate([0, 0, rbottom]) _hooled_toruses(x, y, r, rbottom);
            translate([0, 0, rbottom])
            rcube([x, y, h-rbottom-rtop], r = r, center = false);            
        }
    }
}

module rotate_x(angle) { rotate([angle, 0, 0]) children(); }
module rotate_y(angle) { rotate([0, angle, 0]) children(); }
module rotate_z(angle) { rotate([0, 0, angle]) children(); }

module tr_x(ofs) { translate([ofs, 0, 0]) children(); }
module tr_y(ofs) { translate([0, ofs, 0]) children(); }
module tr_z(ofs) { translate([0, 0, ofs]) children(); }
module tr_xy(ofs_x, ofs_y) { translate([ofs_x, ofs_y, 0]) children(); }

module mirror_x() { mirror([1, 0, 0]) children(); }
module mirror_y() { mirror([0, 1, 0]) children(); }
module mirror_z() { mirror([0, 0, 1]) children(); }

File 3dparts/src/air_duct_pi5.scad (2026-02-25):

include <lib/utils.scad>;
include <lib/nut_trap.scad>;

$fn = $preview ? 64 : 64;

draw_top = 0;
draw_bottom = 0;

wall = 1.5;
wall_base = 2;
bottom_dia = 16;
x = 10;
y = 18;
fan_h = 6.2;
fan_w = 28;
r = 5;

top_dia = 10;
top_h = 11;

mnt_wall = 2;
mnt_hole = 2.2;
mnt_y = 13.5;

module half_sphere (r) {
    difference() {
        sphere(r);
        d = r*2;
        tr_z(-(d+1)/2) cube([d+1, d+1, d+1], center=true);
    }
}

module mount_plate () {
    ra_cube([7, 32, wall_base], r=2);
}

module mount_plate_substract () {
    dupe_y() tr_y(mnt_y) {
        tr_z(-2*e) cylinder(mnt_wall+4*e, d = mnt_hole);

        rotate([0, 0, 38])
        tr_z(mnt_wall+e)
        nut_trap(h=fan_h+mnt_wall, clearance=0);
    }
}

module bottom () {
    difference () {
        union () {
            // body
            hull () {
                difference() {
                    dupe_y() tr_xy(-x/2+r, y/2-r) half_sphere(r + wall);
                    translate([x/2-e, -50, -e]) cube(100);
                }

                dupe_y() tr_xy(x/2, fan_w/2 + wall) cube([e,e, fan_h + wall]);
                dupe_y() tr_xy(x/2-1, fan_w/2 + wall) cube([e,e, fan_h + wall]);
            }

            mount_plate();
        }

        // inner
        translate([e, 0, -e]) hull () {
            dupe_y()
            tr_xy(-x/2+r, y/2-r)
            half_sphere(r);

            dupe_y() tr_xy(x/2, fan_w/2) cube([e,e, fan_h]);
        }

        mount_plate_substract();
    }
}

module top () {
    difference () {
        union () {
            // body
            hull () {
                dupe_y() tr_xy(-x/2+r, y/2-r) cylinder(e, r + wall);

                tr_z(top_h) mirror_z() cylinder(e, r = top_dia/2 + wall);
            }

            mount_plate();

            // orientation key
            tr_x(-x/2 - wall)
            linear_extrude(top_h) hull() {
                square([wall, wall], center = true);
                tr_x(-1.5 + wall/2) circle(d = wall);
            }
        }

        // inner
        tr_z(-e) hull () {
            dupe_y() tr_xy(-x/2+r, y/2-r) cylinder(e, r);
            tr_z(top_h) cylinder(h = 2*e, r = top_dia/2);
        }

        mount_plate_substract();
    }
}

if (!draw_top && !draw_bottom) {
    rotate_x(180) bottom();
    tr_z(2) top();
}

if (draw_top) { top(); }
if (draw_bottom) { bottom(); }

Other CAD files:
3dparts/src/hotplate_80x70x2.8.FCStd
3dparts/mch_head/src/hotplate_tcr_3mch_80x70x2.8.FCStd
3dparts/mch_head/hotplate_tcr_2mch_80x70x2.8.step
3dparts/cap_mjf_pa12.stl
3dparts/src/case.scad
3dparts/button_02.stl
3dparts/hotplate_80x70x2.8.step
3dparts/hotplate_v4_80x70x3.8.step
3dparts/magnet_clamp_75.stl
3dparts/mch_head/src/old/hotplate_rtd_2mch_80x70x2.8.FCStd
3dparts/mch_head/src/old/hotplate_rtd_2mch_80x70x2.8.step
3dparts/mch_head/src/old/ss_mount_2mch_rtd.scad
3dparts/mch_head/src/ss_mount_tcr.scad
3dparts/mch_head/src/thermal_paste_conductor.scad
3dparts/pcb_aligner_03.stl
3dparts/src/drill_conductor.scad
3dparts/src/fan_pi5_data.scad
3dparts/src/magnet_clamp.scad
3dparts/src/pcb_aligner.scad
3dparts/src/ss_mch_mount.scad
3dparts/src/tool_spacer.scad

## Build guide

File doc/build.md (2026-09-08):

Device build <!-- omit in toc -->
============

- [PCB assembly](#pcb-assembly)
- [Firmware upload](#firmware-upload)
- [Heater assembly](#heater-assembly)
- [Case](#case)

## PCB assembly

Use 1 mm locating pins to position the SMT stencil on the PCB. Spread the
solder paste. Apply enough paste to sweep it through the stencil in a single
pass with a plastic card.

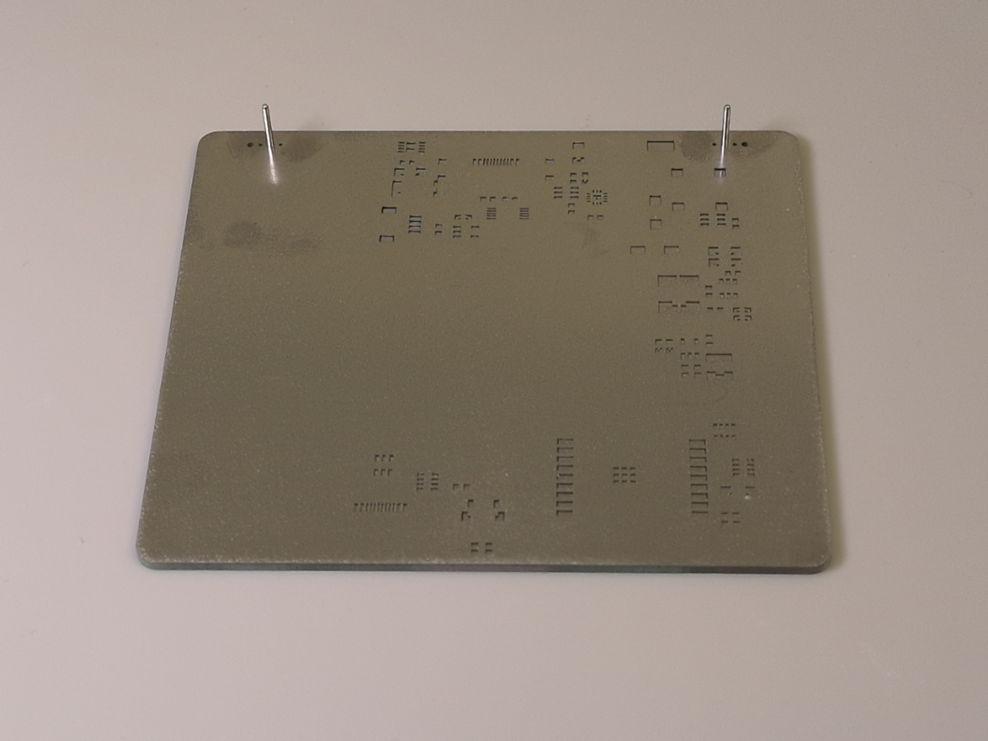
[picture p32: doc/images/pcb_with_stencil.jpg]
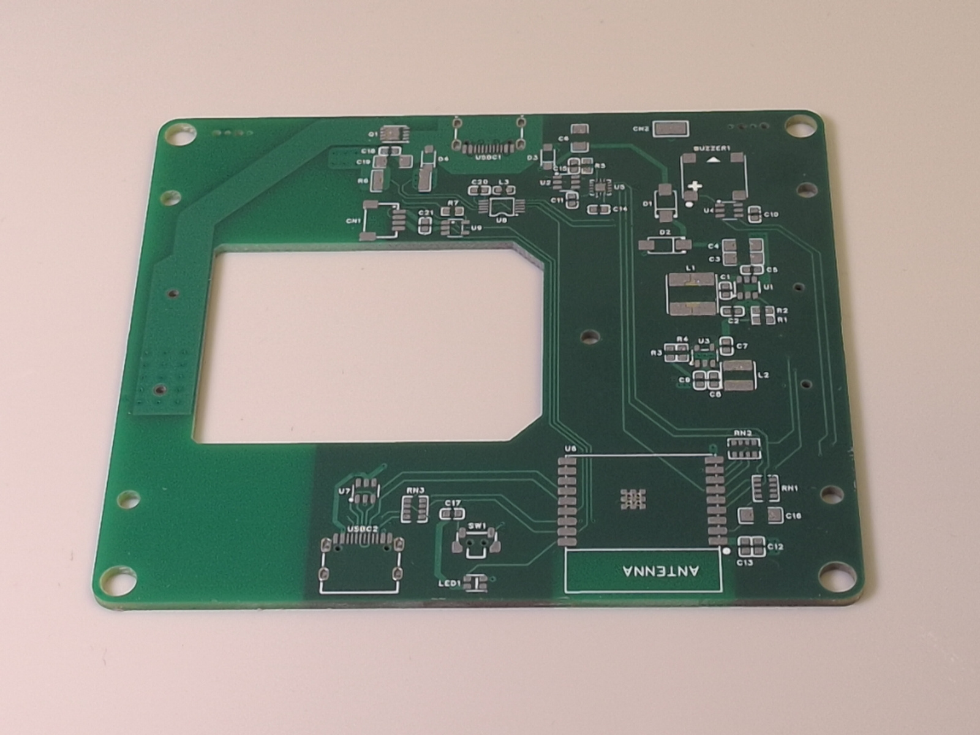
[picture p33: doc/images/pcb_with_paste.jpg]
 

Place the SMD parts and solder everything with a hot-air gun. Inspect the board
and fix any issues with a soldering iron and flux. If you're going to wash the
PCB in an ultrasonic bath, leave the buzzer off until after cleaning to keep it
safe.

Then solder the heating head connectors to the top side of the PCB. Also solder
the USB connector shell tabs.

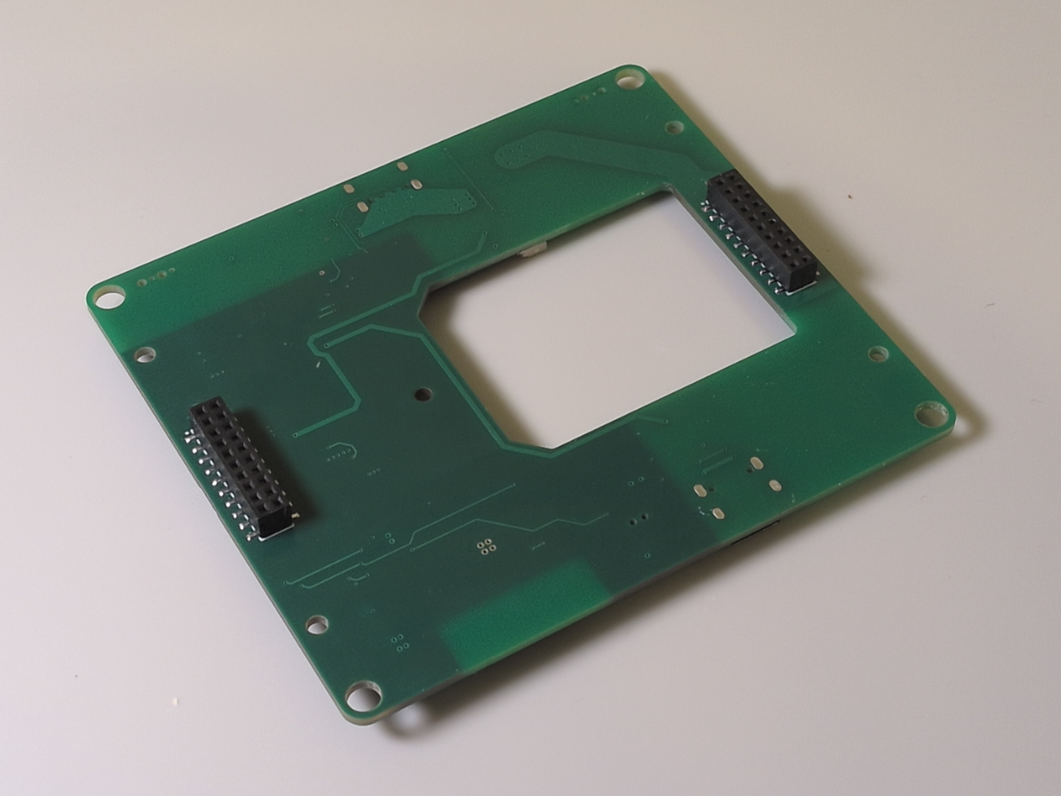
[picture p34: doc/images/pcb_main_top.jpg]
 

> [!TIP]
>
> You can use low-temperature (138°C) paste to keep the process easy and
> minimize mistakes.

When you're done, install the fan and air duct on the PCB cover with the 10 mm
screws.

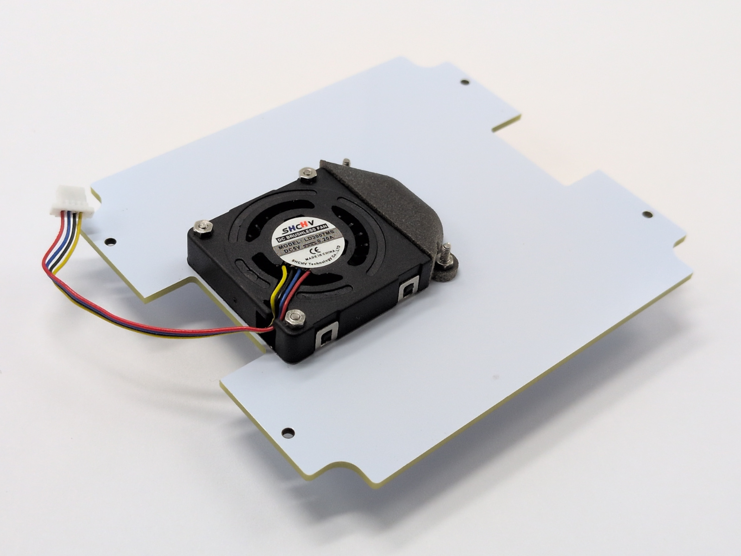
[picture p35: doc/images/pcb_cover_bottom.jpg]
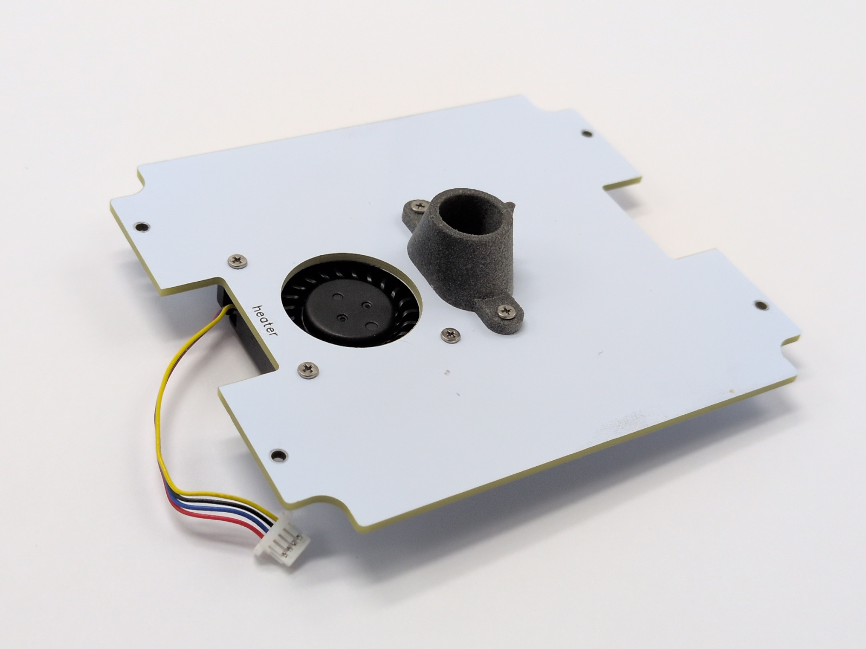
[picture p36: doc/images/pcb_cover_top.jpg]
 

## Firmware upload

1. Install [VS Code](https://code.visualstudio.com/).
2. Clone this repo or download the ZIP archive and unpack it anywhere.
3. Open the `firmware/` folder. When VS Code prompts you to install extensions,
   accept the prompts so PlatformIO and its dependencies are installed.
4. Connect a USB cable to the internal debug connector (next to the LED/button).
5. In VS Code, open the PlatformIO tab (left sidebar), then run
   `PROJECT TASKS` -> `main` -> `General` -> `Upload`. Wait for the build to
   finish; it can take a while. The device beeps when the upload completes.

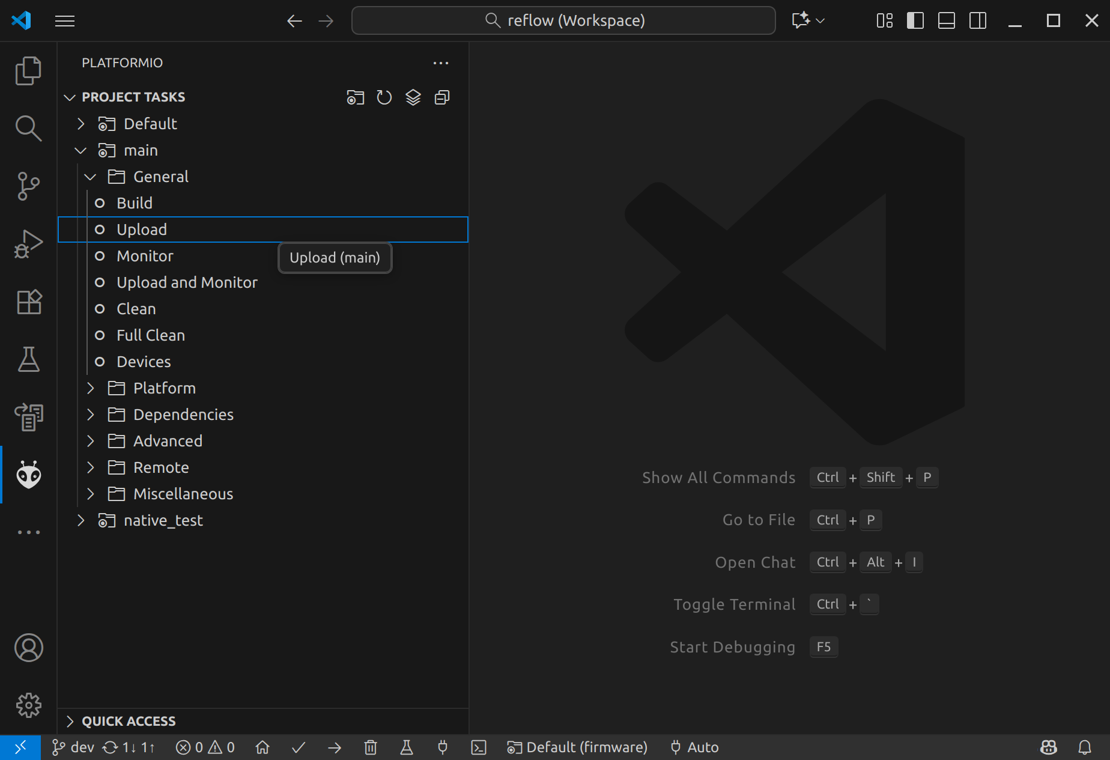
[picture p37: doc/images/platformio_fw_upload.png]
VSCode upload firmware


## Heater assembly

Start by positioning the head connector accurately.

- Place the male connector into the main board sockets. Do not press it in yet.
- Add the alignment conductors at the corners and rest the head base on top.
- Tack the edge pins on the outer side to lock the position.

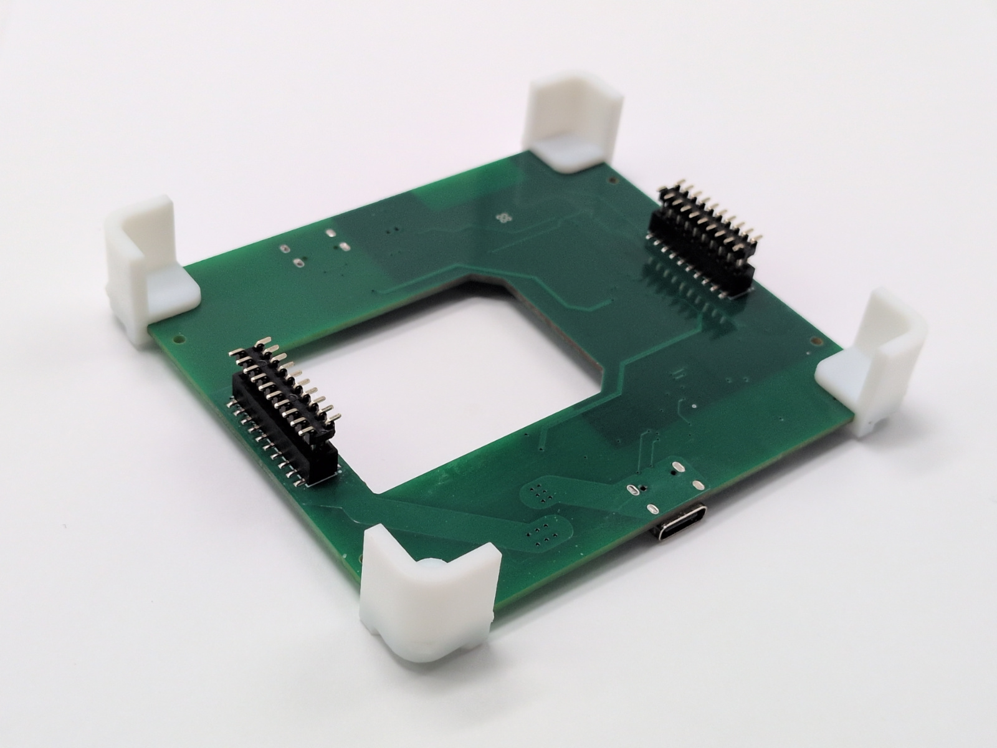
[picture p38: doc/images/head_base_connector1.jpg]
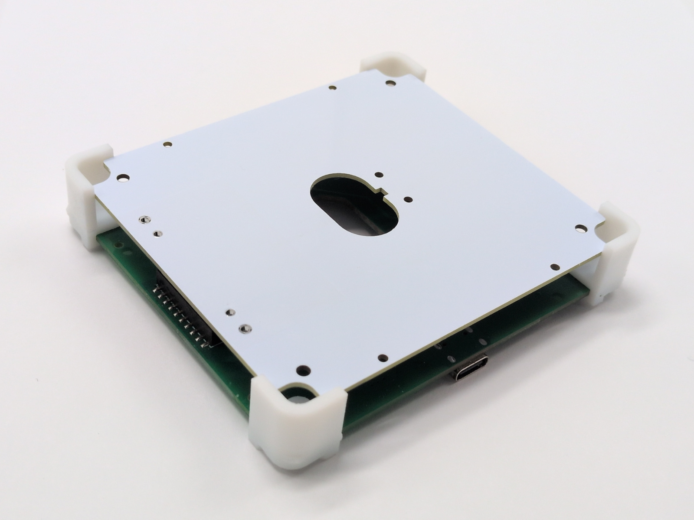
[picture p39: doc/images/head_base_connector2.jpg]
 

Remove the head base, populate the remaining components, and solder them.

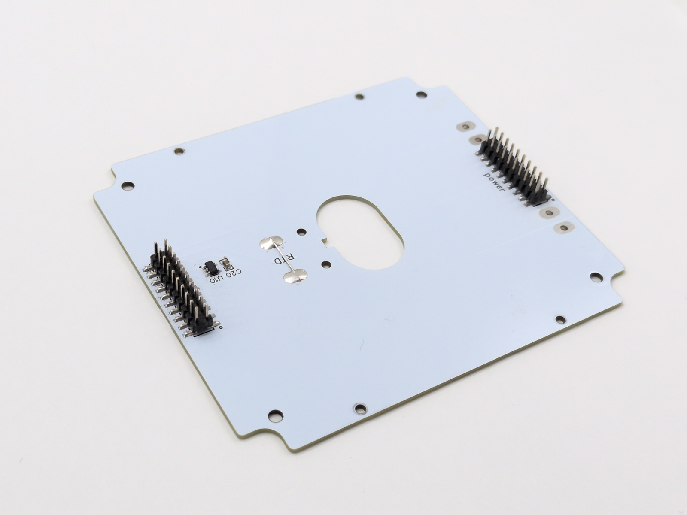
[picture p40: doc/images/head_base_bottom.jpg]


Continue with the hotplate. Countersink the mounting holes with a zero-flute
countersink.

- Set the countersink angle so it touches both rails of the drilling conductor
  evenly. Shift the conductor if needed.
- If you use a screwdriver, countersink freehand while resting the countersink
  on the conductor and pressing through the hole; this keeps the angle correct.
- Run at the lowest speed and clear chips often so they do not scrape the
  conductor.
- Check the depth: insert a screw and slide the conductor above it—the screw
  must not catch on anything.

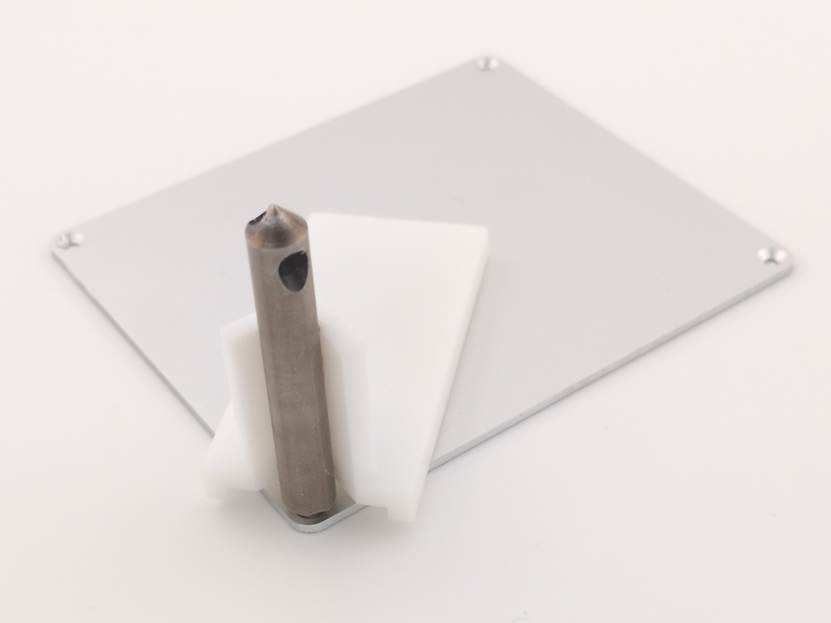
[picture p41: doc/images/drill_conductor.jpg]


Then install the rest of the hotplate components.

- Use 217°C RoHS paste for this step.
- Use AWG 26 (0.4 mm diameter) copper wire for the power lines. The small
  cross-section helps keep heat transfer low.
- If wire is not tinned - tin it first, then solder to the hotplate.
- Use a large iron tip at 350°C to provide enough heat.
- Clean the flux with IPA.
- Install the corner screws with spring washers.

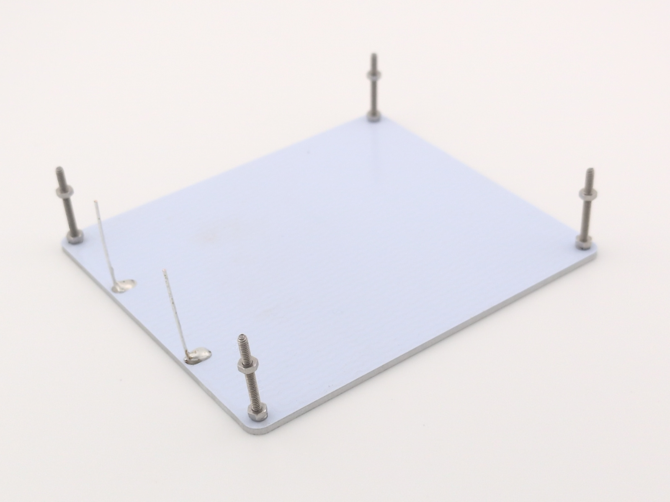
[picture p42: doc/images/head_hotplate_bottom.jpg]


Prepare the foil reflector layer.

- Place the foil on a flat surface with the template on top.
- Cut the foil along the template outline and the central hole with a knife.
- Secure the foil to the template with tape to prevent shifting.
- Punch the mounting holes by pressing through with a screw.
- Clean up the foil burrs around the holes by scraping with a tilted screw.



Install the foil and frame on the hotplate.

- Use spacers to set a 10 mm gap between the heater top and the reflector.
- For each corner, insert the spacer, snug the top nut first, then tighten
  the bottom nut; spring lock washers go underneath.

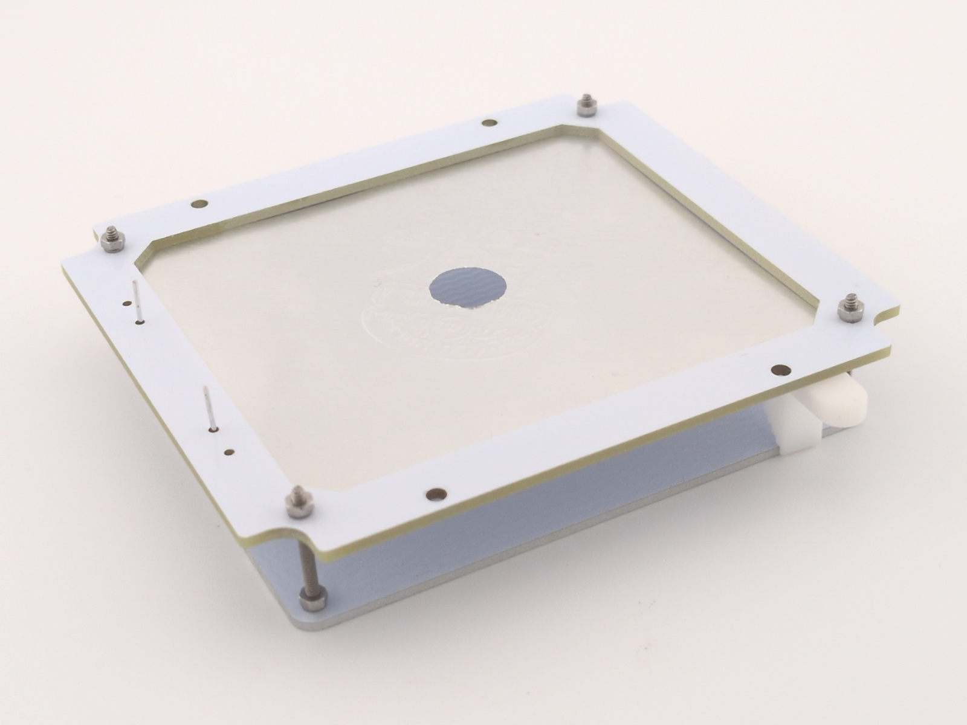
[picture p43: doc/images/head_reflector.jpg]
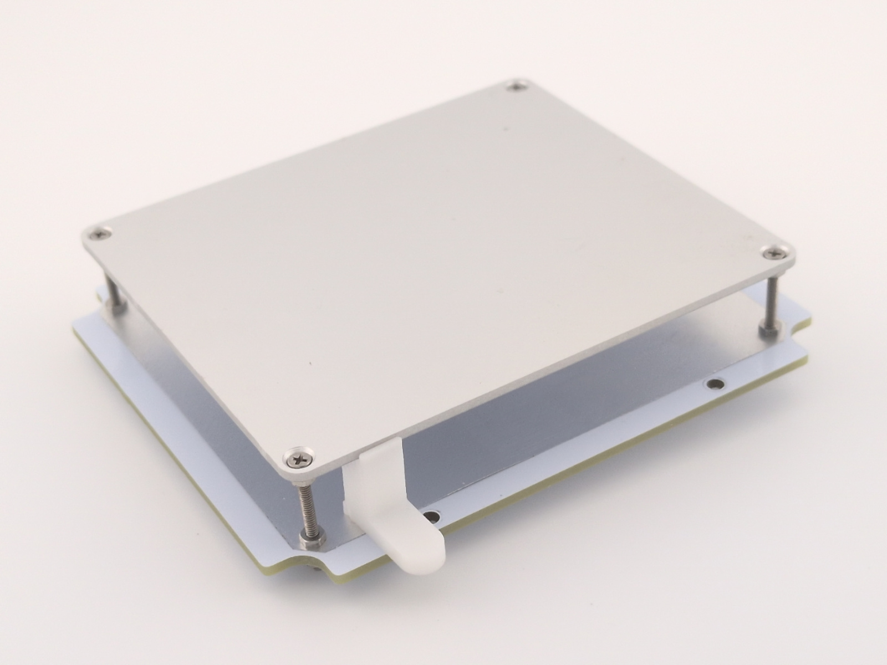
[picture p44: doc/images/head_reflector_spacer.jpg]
 

Attach the hotplate base.

- Install the 4 mm insert nuts into the heating head base using the 3 mm screws.
- Solder the hotplate power wires.
- Clean the flux with IPA.

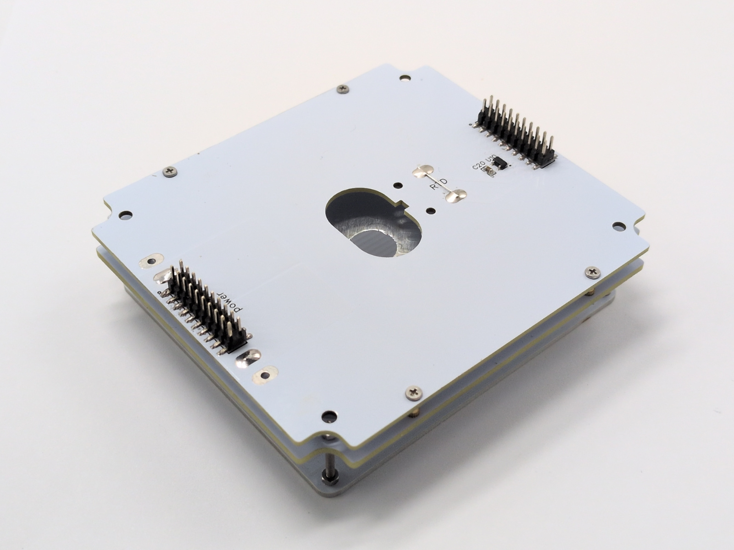
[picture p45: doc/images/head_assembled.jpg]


## Case

### Tray <!-- omit in toc -->

Install the silicone feet on the bottom of the case.

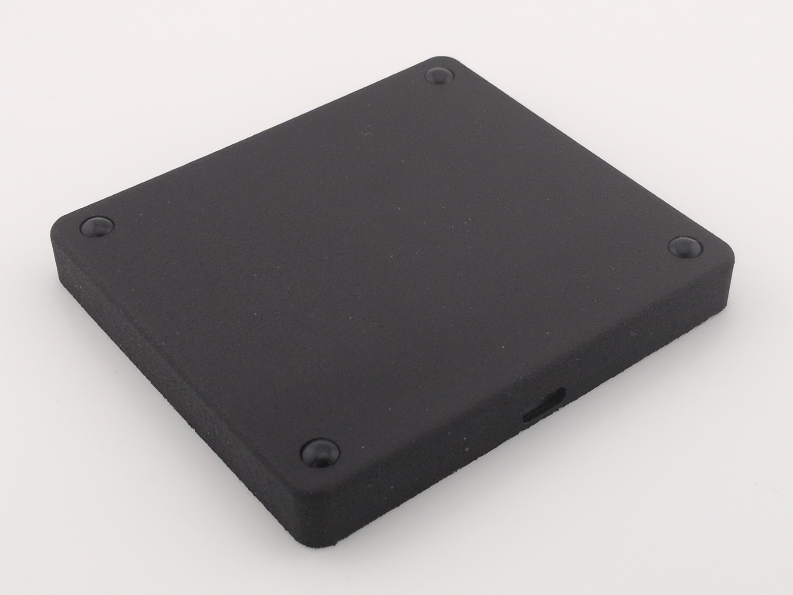
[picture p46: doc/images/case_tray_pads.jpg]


Attach the main PCB to the cover PCB with a screw.

TBD image.

Place the button, nuts, and magnets into the tray.

TBD image.

Then mount the main board and its cover in the tray with the 10 mm screws.



### Cap <!-- omit in toc -->

Install the magnetic screws (black) in the cap and ensure it closes without a
gap. The easiest way is:

- Measure the magnet height above the tray with calipers.
- Set the screw-head depth to the same value plus 0.1 mm of clearance (~ 2.4 mm).
- For a nylon case, just screw them in.
- For an SLA case, stack two layers of electrical tape, cut a 5 mm-wide
  strip, place it inside the screw hole as a shim, then drive the screw in.
  You can add a drop of glue afterward, but it is not mandatory.

TBD image

### Final assembly <!-- omit in toc -->

Then insert the head and you're ready to go!

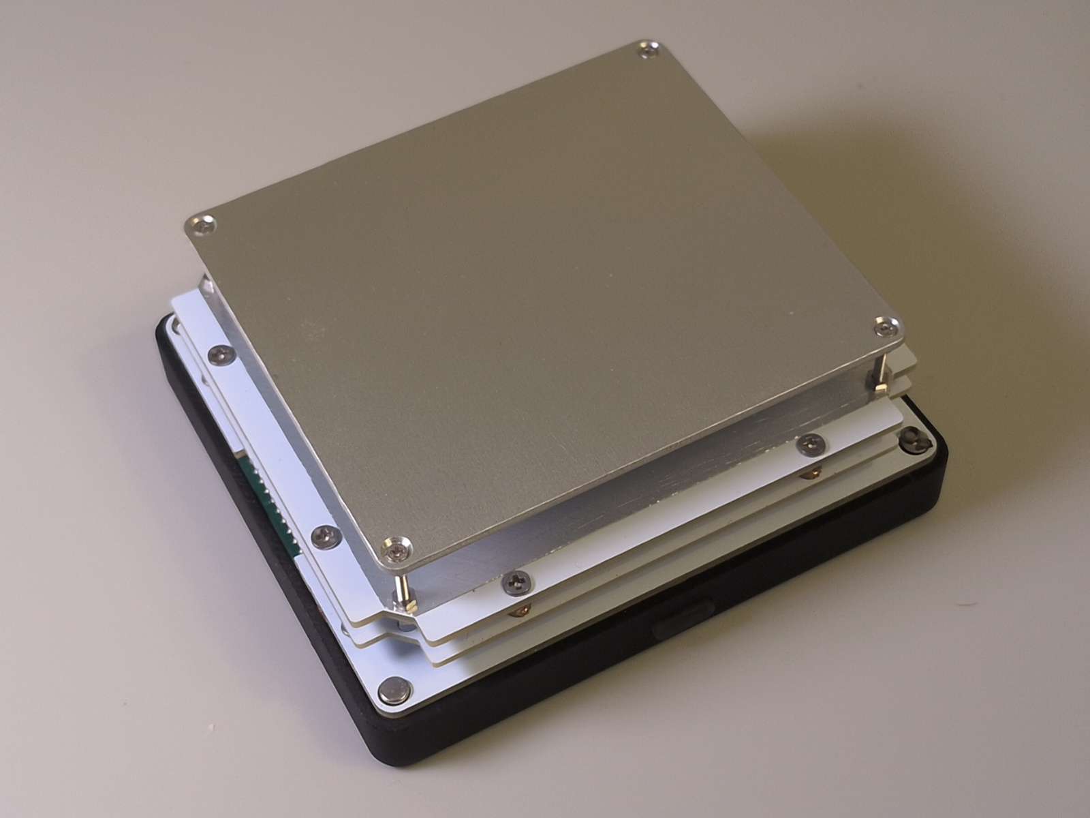
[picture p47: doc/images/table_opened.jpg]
 

Now proceed to [calibration](./calibration.md).

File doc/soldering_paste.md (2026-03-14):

Soldering paste
===============

As explained in [Heating Heads](./heating_heads.md), this reflow table is tuned
for comfortable home use with accessible tools. Here are a few facts about
low-temperature pastes:

1. Keep the operating temperature under 80-90°C. Avoid very hot MOSFETs and
   similar situations.
2. Pure SnBi pastes are brittle; SnBiAg blends hold up better.
3. Avoid high-vibration environments (automotive, frequently dropped devices,
   etc.). That's rarely an issue at home, but for connectors or wires with
   heavy mechanical stress, also consider leaded or standard RoHS solder.
4. AliExpress pastes vary wildly in quality. Buy a known brand like Chip Quik
   whenever you can. Indium is also perfect, but less accessible in small
   quantities.
5. NEVER mix LTS and SnPb solder. That will produce a Rose's-like alloy with a
   very low melting point, causing assembly defects. If you use the same iron
   for both, clear the soldering tip between jobs.

What that means in practice:

- If you gamble on SnBi paste from AliExpress, test it first. It's normal for
  70-80% of random listings to be duds.
- Grab a branded paste like TS391LT when possible, or pick one up from a
  trusted local supplier.

## Some tips

- Store the paste in a syringe. Jars dry out within months after opening, while
  a syringe can keep the paste usable for years.
- If the paste separates because of rough shipping or long storage, don't
  worry. Connect two syringes with a luer-lock adapter and pump the paste back
  and forth a few times. It will mix back to normal.
- Avoid ordering paste at the height of summer when long deliveries sit in high
  heat.

## Applying paste with SMT stencil

- Rule number one: don't be stingy. Load enough paste on the stencil and make a
  single pass with the squeegee. Most problems show up when you try to use too
  little paste and make several passes.
- A plastic card works well as a squeegee.

## Reflow with LTS paste

The default LTS reflow profile in the table has plenty of headroom for most
heavy boards:

- Temperature points are about +10°C higher than usual to cover losses from
  bottom heating.
- The top dwell stretches to 60 seconds.

That profile worked fine on a 4-layer 1.6 mm board with two internal copper
layers. Because LTS paste runs at relatively low temperatures, it's forgiving
and unlikely to overcook the board.

---

> [!NOTE]
>
> This is practical, hobby-focused advice rather than a professional
> process guide.

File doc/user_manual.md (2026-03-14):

User manual
===========

You control everything through the web app. At the moment, Web Bluetooth works
only in Chrome, Edge, and other Chromium-based browsers, so iPhone and iPad
owners should open the app in a desktop browser to access every feature. The
UI is intentionally simple; the short notes below highlight a few useful tricks.

> [!NOTE]
>
> Remember to [calibrate](./calibration.md) each new head before use.

## Install the web app as a "program"

The control page can be saved as a Progressive Web App (PWA), so it behaves
like an installed program. This step is optional—you can always keep using the
usual browser tab—but the shortcut gives one-tap access, opens full-screen, and
keeps working even when the internet connection drops.

### Mobile (Android)

1. Open the web app in Chrome on your Android phone or tablet.
2. Tap **Add to Home Screen** when the banner appears or from the browser menu.
3. Confirm the name (for example, "Reflow Controller") and tap **Add**. The
   home screen icon appears; it opens the app full-screen and keeps running
   even offline. Give it a few seconds—if the icon does not show up right away,
   check the full app list.
4. To remove the shortcut, long-press the icon and pick **Remove/Delete App**.
   Follow the Add to Home Screen flow again if you want it back.

> Safari on iOS still cannot talk over Bluetooth, so use the desktop
> instructions below to control the device from a Mac or PC.

### Desktop (Chrome / Edge / Chromium)

1. Open the web app in Chrome, Edge, or any Chromium-based browser on Windows,
   macOS or Linux.
2. Click the install icon in the address bar (a little monitor or plus sign) or
   open the browser menu and choose **Install App**.
3. Confirm the prompt. The shortcut lands in your apps list, and you can pin it
   to the taskbar or dock.
4. To uninstall, right-click the app icon and choose **Uninstall**, or visit
   **chrome://apps** or **edge://apps** and remove it from there.

## Button control

- **Long-press (about 2 s)** – starts the temperature profile selected in the
  web app.
- **One short press** – stops the run if a profile is active.
- **Five quick presses** – puts the device into Bluetooth pairing mode; do this
  when the web app asks you.

## LED color

- **Green** – idle and ready to start.
- **Yellow → Red → White** – a profile is running; the color shows the
  hotplate temperature (hot / very hot / extremely hot).
- **Blinking blue** – Bluetooth pairing/authentication mode.

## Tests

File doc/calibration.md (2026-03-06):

Calibration
===========

Before you put the head to work, tune two things:

- Temperature sensor.
- Temperature controller.

Both are available from the `Settings` page in the menu.

Every head keeps its own settings in the on-board EEPROM, so you only need to
calibrate it once.

## Temperature sensor

Enter two real-world values: room temperature and the approximate maximum
operating temperature. A basic K-probe thermometer from the BOM is totally
fine.

These budget thermometers can drift by a couple of degrees. That's usually not a
deal-breaker, but if you prefer more accuracy, compare it with a known-good room
thermometer and note the delta. The Xiaomi Mijia BT thermometer, for example,
claims only 0.5°C of error.

Open the app and go to the temperature calibration page.

### Room temperature entry

- Let the thermometer and device sit for 15 minutes with no drafts. Turn off
  the air conditioner if it's running.
- Enter the thermometer reading (Point 1).

After this step the web app will be close to the real temperature, but you still
need the second point.

### Max temperature entry

Now you need to bake the sensor a bit below the maximum operating value.

- 170°C for the PCB-based heater, about 25 W.
- 250°C for the MCH-based heater, about 50 W.

Don't exceed that temperature, or you can damage the heater.

- Set the recommended power and press `Bake`.
- Wait for the temperature to stabilize. It can take 10-15 minutes.
- Monitor the temperature with the thermometer through a solder drop and tweak
  the power if needed.
- Enter the Point 2 value.

*Tip: Measuring through a solder drop gives the probe a better contact area.
Touching the plate directly with the small K-type bead leads to noticeable
errors.*

## Temperature controller

The default settings are for the MCPCB-based heater, so there's a good chance
you won't need to touch the ADRC values.

For an MCH-based heater, or if you change the heater size, follow the
instructions below.

- Enable debug info on the `Settings` page.

### Run a step response test

This automatically estimates the head response time and scale factor.

- Wait until the hotplate cools back to room temperature. If it was warm, give
  it 10-15 minutes, or use the cooling fan.
- In the `Auto tuning` section, set the power as you did for the sensor bake.
  Press `Run` and wait for it to finish.

### Tune N/M parameters

- Set `M` = 2 and don't change it.
- In the `Test controller` section, set the temperature to the main working
  range for the heater type (170-210°C), and press `Run`.
- When the temperature stabilizes, start increasing `N` from 10 until you see
  power jitter above 20% in the debug info.
- After jitter appears, reduce `N` by 10-20%.

Usually, these values are OK:

- MCPCB head: `M = 2`, `N = 50`.
- MCH head: `M = 2`, `N = 60`.

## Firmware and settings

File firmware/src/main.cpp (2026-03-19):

#include <etl/error_handler.h>
#include "app.hpp"
#include "components/prefs.hpp"
#include "components/stack_monitor.hpp"
#include "logger.hpp"
#include "rpc/rpc.hpp"

void etl_error_log(const etl::exception& e) {
    APP_LOGE("ETL Error: {}, file: {}, line: {}",
        e.what(), e.file_name(), e.line_number());
}

extern "C" void app_main(void) {
    logger_start();

#ifdef ETL_LOG_ERRORS
    etl::error_handler::set_callback<etl_error_log>();
#endif

    PrefsWriter::getInstance().setup();

    application.setup();

    rpc_start();

    //stack_monitor_start();

    // Main task no longer needed once initialization completes.
    vTaskDelete(nullptr);
}

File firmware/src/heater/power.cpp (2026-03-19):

#include <pd/pd.h>

#include "app.hpp"
#include "app_dpm.hpp"
#include "drain_tracker.hpp"
#include "logger.hpp"
#include "power.hpp"

ProfileSelector profile_selector;

pd::Port port;
Power power;

pd::fusb302::Fusb302RtosHalEsp32 fusb302_hal;
pd::fusb302::Fusb302Rtos driver{port, fusb302_hal};

pd::Task task{port, driver};
AppDPM dpm{port, power};
pd::PRL prl{port, driver};
pd::PE pe{port, dpm, prl, driver};
pd::TC tc{port, driver};

namespace PWR_STATE {
    enum {
        Off,
        Initializing,
        Calibrate,
        Ready,
        WaitContractChange,
        Fault
    };
}

namespace {
    constexpr auto pwr_state_to_desc(int state) -> const char* {
        switch (state) {
            case PWR_STATE::Off: return "Off";
            case PWR_STATE::Initializing: return "Initializing";
            case PWR_STATE::Calibrate: return "Calibrate";
            case PWR_STATE::Ready: return "Ready";
            case PWR_STATE::WaitContractChange: return "WaitContractChange";
            case PWR_STATE::Fault: return "Fault";
            default: return "Unknown";
        }
    }
}

#define HANDLE_UNKNOWN_EVENT \
    auto on_event_unknown(const etl::imessage& event) -> etl::fsm_state_id_t { \
        return No_State_Change; \
    }


class PowerOff_State : public etl::fsm_state<Power, PowerOff_State, PWR_STATE::Off> {
public:
    HANDLE_UNKNOWN_EVENT;

    auto on_enter_state() -> etl::fsm_state_id_t override {
        auto& pwr = get_fsm_context();
        pwr.log_state();

        pwr.source_caps.clear();
        profile_selector.descriptors.clear();
        profile_selector.set_pdo_index(0);
        pwr.pwm.enable(false);
        drain_tracker.reset();
        pwr.target_power_mw = 0;
        pwr.set_power_status(PowerStatus::PowerStatus_PWR_OFF);
        application.enqueue_message(AppCmd::Stop{});
        return No_State_Change;
    }
};

class PowerInitializing_State : public etl::fsm_state<Power, PowerInitializing_State, PWR_STATE::Initializing,
    pd::MsgToDpm_HandshakeDone, pd::MsgToDpm_SnkReady> {
public:
    HANDLE_UNKNOWN_EVENT;

    auto on_enter_state() -> etl::fsm_state_id_t override {
        auto& pwr = get_fsm_context();
        pwr.log_state();

        auto& ps = profile_selector;
        dpm.clear_trigger_to(ps.default_position, ps.default_mv);

        pwr.pwm.enable(false);
        drain_tracker.reset();
        pwr.target_power_mw = 0;
        pwr.set_power_status(PowerStatus::PowerStatus_PWR_INITIALIZING);
        application.enqueue_message(AppCmd::Stop{});
        return No_State_Change;
    }

    auto on_event(const pd::MsgToDpm_HandshakeDone&) -> etl::fsm_state_id_t {
        return PWR_STATE::Calibrate;
    }

    auto on_event(const pd::MsgToDpm_SnkReady&) -> etl::fsm_state_id_t {
        if (port.pe_flags.test(pd::PE_FLAG::HANDSHAKE_REPORTED)) {
            return PWR_STATE::Calibrate;
        }
        return No_State_Change;
    }
};

class PowerCalibrate_State : public etl::fsm_state<Power, PowerCalibrate_State, PWR_STATE::Calibrate,
    MsgToPower_SysTick> {
public:
    HANDLE_UNKNOWN_EVENT;

    auto on_enter_state() -> etl::fsm_state_id_t override {
        auto& pwr = get_fsm_context();
        pwr.log_state();
        if (drain_tracker.get_info().load_valid) {
            return PWR_STATE::Ready;
        }

        pwr.pwm.set_duty_x1000(0);
        pwr.pwm.enable(true);
        return No_State_Change;
    }

    auto on_event(const MsgToPower_SysTick&) -> etl::fsm_state_id_t {
        if (drain_tracker.get_info().load_valid) {
            return PWR_STATE::Ready;
        }

        return No_State_Change;
    }
};

class PowerReady_State : public etl::fsm_state<Power, PowerReady_State, PWR_STATE::Ready,
    MsgToPower_SysTick, pd::MsgToDpm_SnkReady, pd::MsgToDpm_NewPowerLevelRejected, pd::MsgToDpm_SrcCapsReceived> {
public:
    HANDLE_UNKNOWN_EVENT;

    auto on_enter_state() -> etl::fsm_state_id_t override {
        auto& pwr = get_fsm_context();
        pwr.log_state();

        pwr.set_power_status(PowerStatus::PowerStatus_PWR_OK);
        // Reset lock for sure
        pwr.is_apdo_updating = false;
        pwr.prev_apdo_mv = 0;
        // Don't start PWM/Profile here, wait for SysTick to kick in.
        // This will cause small delay on first entry, but that's acceptable.
        return No_State_Change;
    }

    auto on_event(const pd::MsgToDpm_NewPowerLevelRejected&) -> etl::fsm_state_id_t {
        auto& pwr = get_fsm_context();
        auto& ps = profile_selector;

        // Local APDO update failed
        pwr.is_apdo_updating = false;
        // Force re-init on failure
        // NOTE: trigger function MUST be async to avoid deadlock
        dpm.trigger_by_position(ps.default_position, ps.default_mv);
        return PWR_STATE::Initializing;
    }

    // If SRC forced capabilities or soft reset (followed by capabilities)
    auto on_event(const pd::MsgToDpm_SrcCapsReceived&) -> etl::fsm_state_id_t {
        auto& pwr = get_fsm_context();

        APP_LOGI("Power: got unexpected src caps, restore profile selection...");
        pwr.is_from_caps_update = true;
        return PWR_STATE::WaitContractChange;
    }

    auto on_event(const pd::MsgToDpm_SnkReady&) -> etl::fsm_state_id_t {
        auto& pwr = get_fsm_context();

        // Local APDO update complete, and SRC is ready.
        // PWM stays intact, because been updated prior to APDO adjusting.
        pwr.prev_apdo_mv = pwr.next_apdo_mv;
        pwr.current_plan = pwr.next_plan;
        pwr.is_apdo_updating = false;
        return No_State_Change;
    }

    auto on_event(const MsgToPower_SysTick&) -> etl::fsm_state_id_t {
        auto& pwr = get_fsm_context();
        auto& ps = profile_selector;

        auto drain_info = drain_tracker.get_info();
        auto consumer_valid = drain_info.load_valid;

        if (consumer_valid) {
            // Update feedback with current measurements.
            // Context from current_plan — that's what was active during measurement.
            ProfileSelector::FEEDBACK_PARAMS fb{
                .peak_mv = drain_info.peak_mv,
                .peak_ma = drain_info.peak_ma,
                .req_mv = pwr.current_plan.mv,
                .req_idx = pwr.current_plan.profile_idx
            };
            pwr.last_feedback = fb;
        }

        if (pwr.is_apdo_updating) {
            // Wait until APDO update is finished
            return No_State_Change;
        }

        if (!consumer_valid) {
            // If head connection lost for some reasons (ejected)
            pwr.pwm.enable(false);
            // NOTE: trigger function MUST be async to avoid deadlock
            dpm.trigger_by_position(ps.default_position, ps.default_mv);
            return PWR_STATE::Initializing;
        }

        auto plan = ps.plan_power(pwr.target_power_mw, pwr.last_feedback);
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

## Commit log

2024-05-10 Rework 3d parts
    [case.scad, case_v1_old.scad, hotplate_v1_70x60.FCStd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]
2024-05-10 Add 3d production files
    [button.stl, cap.stl, hotplate_v1_70x60.step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]
2024-06-29 Drop 3mm plate
    [hotplate_v2_80x70x3.FCStd, hotplate_v2_80x70x3.step]
2024-06-29 Update PCB mounting and tools
    [cap.stl, case.scad, tool_foil_conductor.scad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]
2024-06-29 Hotplate: add chamfer on top
    [hotplate_v3_80x70x4.FCStd, hotplate_v3_80x70x4.step]
2024-06-30 case: tweak sizes
    [case_v2_old.scad]
2024-06-30 case: add stiffeners
    [case.scad]
2024-06-30 case: remove sharp angles in magnet holders
    [case.scad]
2024-06-30 Add PCB aligner for connectors mount
    [tool_aligner.scad, tool_aligner.stl]
2024-06-30 case: button rework
    [case.scad]
2024-06-30 case: simplify magnet supports
    [case.scad]
2024-06-30 stl update
    [button.stl, cap.stl, tray.stl]
2024-07-24 Add air duct
    [air_duct.scad, air_duct.stl, air_duct_alt.stl]
2024-07-24 Updated hotplate
    [hotplate_v4_80x70x3.8.FCStd, hotplate_v4_80x70x3.8.step]
2024-08-05 Rework air duct to pi5 fan
    [air_duct.stl, air_duct_1703.scad, air_duct_alt.stl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]
2024-08-05 Alt v4 hotplate, without bottom chamfer
    [hotplate_v4_80x70x3.8_alt.FCStd, hotplate_v4_80x70x3.8_alt.step]
2024-08-05 More auxiliary equipment + group clones to reduce print price
    [magnet_clamp.scad, magnet_clamp_75.stl, magnet_clamp_80.stl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]
2024-08-05 Partial tray rework
    - Increase inner to 8mm for new fan
    - rework USB (increase hole)
    - increase led space for ws2812b
    - add bottom heels
    [case.scad]
2024-08-05 Add button variants for PA12
    [button_03.stl, button_04.stl, button_05.stl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]
2024-08-05 tray: add fan+ mounting space
    [case.scad]
2024-08-06 rework magnets & cap
    [case.scad]
2024-08-06 update stl builder script
    [air_duct_pi5_bottom.stl, cap_alt.stl, case.scad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]
2024-08-07 magnet clamps rework
    [magnet_clamp.scad, magnet_clamp_70.stl, magnet_clamp_80.stl]
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2024-08-20 Update hotplate
    [hotplate_80x70x2.8.FCStd, hotplate_80x70x2.8.step, hotplate_80x70x3.8.FCStd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]
2024-08-21 Drop outdated files
    [case_v1_old.scad, case_v2_old.scad, tool_aligner.scad]
2024-08-21 3d[arts: update clamps & aligners
    [magnet_clamp.scad, magnet_clamp.stl, magnet_clamp_70.stl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]
2024-08-26 cnc: added pt100 mounting
    [hotplate_80x70x2.8.FCStd, hotplate_80x70x2.8.step, hotplate_80x70x3.8.FCStd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]
2024-08-26 case: improve magnet holders
    [case.scad]
2024-08-28 tray: usb hole update
    [case.scad]
2024-08-28 Added stainless steel mch mounting
    [ss_mch_mount.scad, ss_mch_mount.stl]
2024-08-28 tray: increase pi5 fan holes
    [case.scad]
2024-08-29 button tweak
    [button.stl, button_02.stl, button_03.stl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]
2024-08-29 Add mounting washer
    [ss_mch_mount.scad]
2024-08-30 Add space for fan wires
    [case.scad, tray.stl]
2024-09-16 Update ss mounting to fit manufacturing limits
    [ss_mch_mount.scad]
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2024-11-18 3D: finalize button
    [button.stl, button_03.stl]
2024-11-18 Add duct variants
    [air_duct_pi5.scad, air_duct_pi5_top_10.stl, air_duct_pi5_top_11.stl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]
2024-11-23 3D: rework ss clamps and washers.
    [ss_mch_mount.scad, ss_mch_mount.stl]
2024-11-23 3D: update hotplate RTD mounting
    [hotplate_80x70x2.8.FCStd, hotplate_80x70x2.8.step]
2024-11-24 3D: Revert extra space for fan screw
    [case.scad]
2024-11-24 3D: Increase USB hole round radius
    [case.scad, tray.stl]
2024-11-26 3d: update ss print bridges to match jlc3dp requirements
    [ss_mch_mount.scad, ss_mch_mount.stl]
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2024-12-12 3d: tweak ss clamps thickness and bridges
    [ss_mch_mount.scad, ss_mch_mount.stl]
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2024-12-20 Rework blinker/button/app classes
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2024-12-24 Rework DeviceState & add validators
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2024-12-29 Rework prefs init to more strict
    [main.cpp]
2024-12-29 cs: fix some cpp_check reports
    [main.cpp]
2024-12-29 CS: fix type conversion
    [main.cpp]
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2025-01-04 fw: fix status/history comm
    [main.cpp]
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2025-01-07 fw: fix heater model params setup
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2025-04-08 Added head orientation key
    [air_duct_pi5.scad, air_duct_pi5_top_10.stl, air_duct_pi5_top_11.stl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]
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2025-04-26 3d: tray, remove fan screws inlets
    [case.scad, tray.stl]
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2025-06-16 3d: added conductor for PCB-based experimental hotplate
    [drill_conductor.scad, drill_conductor.stl]
2025-06-16 3d: remove fan connector extra space
    [case.scad, tray.stl]
2025-06-19 3d: added cap logo
    [MinkowskiRound.scad, case.scad, polyround.scad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]
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2025-06-25 Added buzzer rtttl player
    [buzzer.cpp]
2025-06-28 3d: increase btn protrusion & round edges.
    [air_duct_1703.scad, air_duct_pi5.scad, button.stl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]
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2025-06-30 fw: modify structs init to avoid warnings on sdk version change.
    [buzzer.cpp, fan.cpp]
2025-07-15 3d: stabilize stl output
    [air_duct_pi5_bottom.stl, air_duct_pi5_top_10.stl, air_duct_pi5_top_11.stl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]
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2025-08-19 3d: return back fan screws extra space
    [case.scad, tray.stl]
2025-08-20 3d: increase space for insert nuts
    [case.scad, tray.stl]
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2025-09-06 fw: add ETL error log
    [main.cpp]
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2025-09-07 fix ledc warnings
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2025-09-13 fw: fix eeprom write delay
    [eeprom_store.cpp]
2025-09-13 fw: refactor ADC read to retry on errors
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2025-09-20 3d: add guides to simplify cap opening
    [case.scad]
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2025-09-28 Fix i2c init and minor code polish
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2025-09-29 fw: fix BLE name in browser device connection dialog
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2025-10-19 fw: fix fan logic
2025-10-20 fw: fix sensor baking task sounds
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2025-11-01 webL display head/power errors on main page
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2025-11-05 web: add head capacity correction to simulator
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2025-11-09 3d: change pcb mounting holes for m2 and add heat insert variant
    [case.scad, tray.stl, tray_insert_3.25.stl]
2025-11-10 3d: update drill conductor for countersink
    [drill_conductor.scad, drill_conductor.stl]
2025-11-10 3d: add button diffuser for the led
    [button.stl, case.scad]
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2025-11-14 3d: remove unised stl variants
    [air_duct_pi5_top.stl, air_duct_pi5_top_10.stl, air_duct_pi5_top_straight_10.stl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]
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2025-11-20 web: fix power status error display
2025-11-26 Refactor MCH files, add 3-MCH variant draft
    [hotplate_rtd_2mch_80x70x2.8.FCStd, hotplate_rtd_2mch_80x70x2.8.step, hotplate_tcr_2mch_80x70x2.8.FCStd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]
2025-12-10 fw: properly restore power state after PD Soft Reset (when unexpected source capabilities received)
    [power.cpp]
2025-12-11 fw: fix HeaterControl tick time delta math and related things
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2025-12-21 Fix ADRC parametrization and calibration info
2025-12-21 3d: remove fan mounting extra space and reduce pocket for rubber feets
    [case.scad, tray.stl, tray_insert_3.25.stl]
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2025-12-24 fw: fix b1da675 regression: pwm disable should not invalidate drain_tracker data.
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2026-01-01 Add 2 mm mounting variant for air duct
    [air_duct_pi5.scad]
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2026-01-05 3d: air duct update
    [air_duct_pi5.scad, air_duct_pi5_bottom.stl, air_duct_pi5_top.stl]
2026-02-25 Rework case lock, BOM, and related things
    [air_duct_pi5.scad, air_duct_pi5_bottom.stl, air_duct_pi5_top.stl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]
2026-02-26 fw: add ina238 support & fix ina226 config
    [drain_tracker.cpp]
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2026-02-26 fw: use ina238 with hw average to reduce the noise
    [drain_tracker.cpp]
2026-02-27 grammar fixes
    [case.scad]
2026-03-06 Add thermal paste stencil and polish bom
    [thermal_paste_conductor.scad, thermal_paste_conductor.stl]
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2026-03-25 3d: adjust thermal paste conductor
    [thermal_paste_conductor.scad, thermal_paste_conductor.stl]
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2026-04-12 3d: shift 1mm down tray nut holes
    [case.scad]
2026-04-12 3d: adjust button hole
    [case.scad, tray.stl]
2026-04-26 3d: finalize cap screw hole size
    [cap_sla.stl, case.scad]
